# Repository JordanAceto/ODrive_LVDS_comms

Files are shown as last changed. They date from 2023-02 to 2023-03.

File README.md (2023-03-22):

# Set of small PCBs for Odrive ◄► motor encoder comms

- One board sits on an Odrive
- The other goes inside a gimbal motor
- They are connected with twisted pair wire
- The goal is to increase noise immunity and have convenient connectors
- One Odrive board can connect to two encoder boards

---

### Connectors used
- JST GH series 9 pin

---

### IMPORTANT NOTE 1
- The encoder board PCB should be 1mm thick
- The ODRive board can be any thickness you like

---

### IMPORTANT NOTE 2
- The two SN65LVDS050PW chips on the ODrive board will conflict if you use only one motor at a time
- Setting the chip select line high for a given SN65LVDS050PW chip puts its SDI pin into a high impedance state
- If the chip select line is low or not active, the SN65LVDS050PW chip will assert its output on the shared SDI line
- When using only 1 motor there are two options:
  - set the chip select line for the unused SN65LVDS050PW permanently high
  - only solder one SN65LVDS050PW chip

---

### Status
- test build done, safe to order boards

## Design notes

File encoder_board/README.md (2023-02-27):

# encoder_board




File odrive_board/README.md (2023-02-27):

# odrive_board




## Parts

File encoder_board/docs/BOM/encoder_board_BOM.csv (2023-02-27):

# | Reference | Qty | Value | Footprint | DNP
1 | C1 | 1 | 10µF | Capacitor_SMD:C_0603_1608Metric
2 | C2 | 1 | 100nF | Capacitor_SMD:C_0603_1608Metric
3 | C3 | 1 | 100n | Capacitor_SMD:C_0603_1608Metric
4 | C4 | 1 | 1n | Capacitor_SMD:C_0603_1608Metric
5 | J1 | 1 | TO_ODRIVE | Connector_JST:JST_GH_SM09B-GHS-TB_1x09-1MP_P1.25mm_Horizontal
6 | R1 | 1 | 620 | Resistor_SMD:R_0603_1608Metric
7 | R2, R3 | 2 | 110 | Resistor_SMD:R_0603_1608Metric
8 | U1 | 1 | AS5048A | Package_SO:TSSOP-14_4.4x5mm_P0.65mm
9 | U2 | 1 | SN65LVDS050PW | Package_SO:TSSOP-16_4.4x5mm_P0.65mm

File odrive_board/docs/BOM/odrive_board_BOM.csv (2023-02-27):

# | Reference | Qty | Value | Footprint | DNP
1 | C1, C3 | 2 | 100n | Capacitor_SMD:C_0603_1608Metric
2 | C2, C4 | 2 | 1n | Capacitor_SMD:C_0603_1608Metric
3 | J1 | 1 | Odrive_conn | Connector_PinHeader_2.54mm:PinHeader_1x20_P2.54mm_Vertical
4 | J2 | 1 | thru_conn | Connector_PinHeader_2.54mm:PinHeader_1x20_P2.54mm_Vertical
5 | J3 | 1 | MOTOR_0 | Connector_JST:JST_GH_SM09B-GHS-TB_1x09-1MP_P1.25mm_Horizontal
6 | J4 | 1 | MOTOR_1 | Connector_JST:JST_GH_SM09B-GHS-TB_1x09-1MP_P1.25mm_Horizontal
7 | R1, R2 | 2 | 110 | Resistor_SMD:R_0603_1608Metric
8 | TP1 | 1 | SCK | TestPoint:TestPoint_Keystone_5000-5004_Miniature
9 | TP2 | 1 | SDI | TestPoint:TestPoint_Keystone_5000-5004_Miniature
10 | TP3 | 1 | SDO | TestPoint:TestPoint_Keystone_5000-5004_Miniature
11 | TP4 | 1 | CS_0 | TestPoint:TestPoint_Keystone_5000-5004_Miniature
12 | TP5 | 1 | CS_1 | TestPoint:TestPoint_Keystone_5000-5004_Miniature
13 | TP6 | 1 | 3V3 | TestPoint:TestPoint_Keystone_5000-5004_Miniature
14 | TP7 | 1 | GND | TestPoint:TestPoint_Bridge_Pitch5.08mm_Drill0.7mm
15 | U1, U2 | 2 | SN65LVDS050PW | Package_SO:TSSOP-16_4.4x5mm_P0.65mm

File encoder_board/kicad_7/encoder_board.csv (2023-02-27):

# | Reference | Qty | Value | Footprint | DNP
1 | C1 | 1 | 10µF | Capacitor_SMD:C_0603_1608Metric
2 | C2 | 1 | 100nF | Capacitor_SMD:C_0603_1608Metric
3 | C3 | 1 | 4u7 | Capacitor_SMD:C_0603_1608Metric
4 | C4 | 1 | 1u | Capacitor_SMD:C_0603_1608Metric
5 | J1 | 1 | TO_ODRIVE | Connector_JST:JST_GH_SM07B-GHS-TB_1x07-1MP_P1.25mm_Horizontal
6 | R1, R3, R4 | 3 | 620 | Resistor_SMD:R_0603_1608Metric
7 | R2 | 1 | 110 | Resistor_SMD:R_0603_1608Metric
8 | U1 | 1 | AS5048A | Package_SO:TSSOP-14_4.4x5mm_P0.65mm
9 | U2 | 1 | LTC4332 | Package_DFN_QFN:QFN-20-1EP_4x5mm_P0.5mm_EP2.65x3.65mm

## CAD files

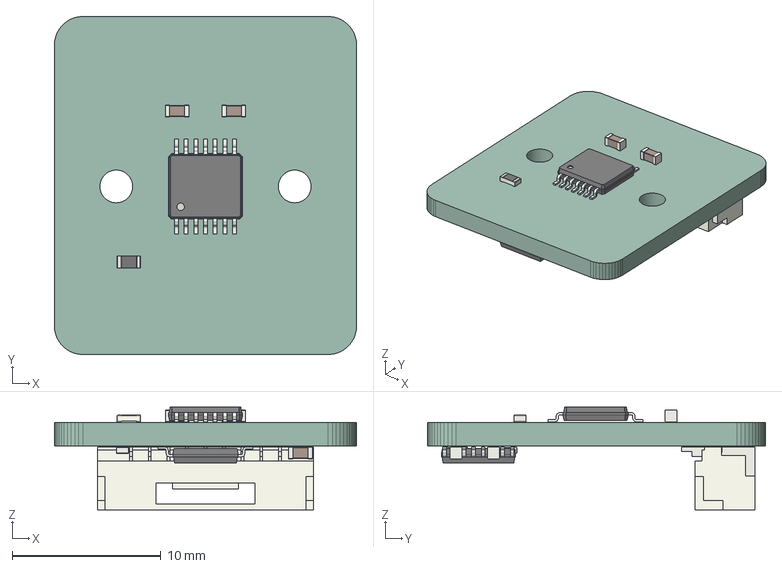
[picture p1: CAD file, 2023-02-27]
encoder_board/docs/3D/encoder_board.step
20.3 x 22.7 x 6.92 mm
PCB

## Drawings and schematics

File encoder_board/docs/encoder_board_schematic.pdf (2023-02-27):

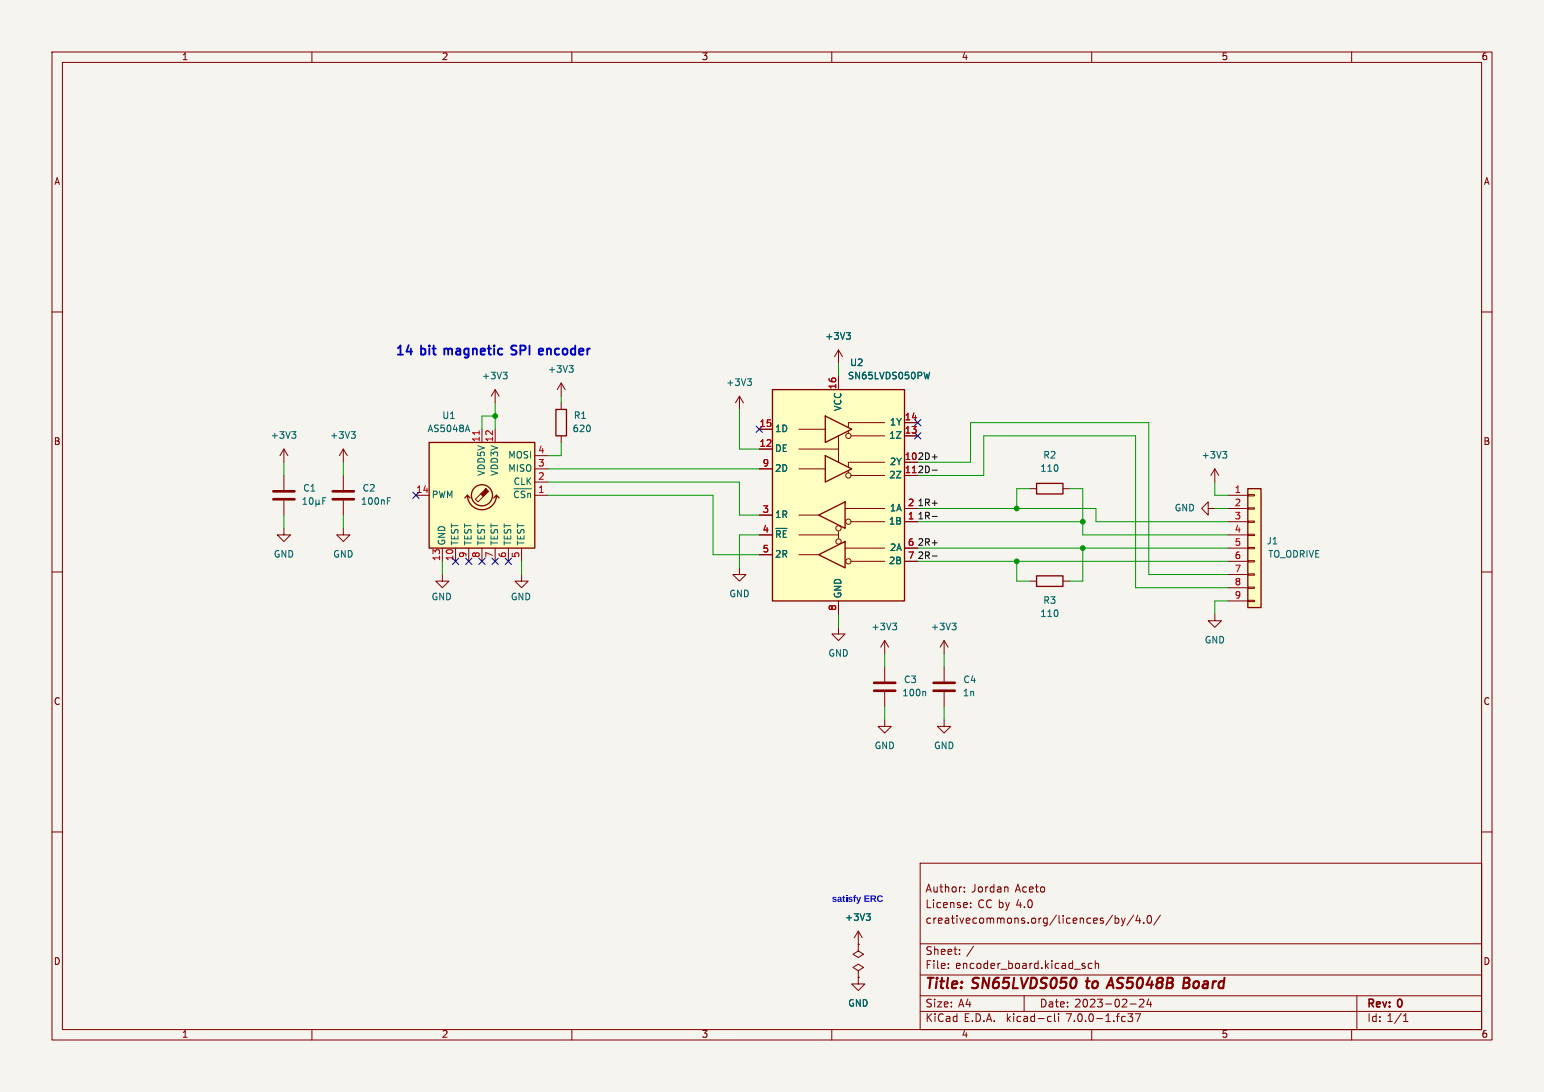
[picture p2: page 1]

Id: 1/1 Title: SN65LVDS050 to AS5048B Board

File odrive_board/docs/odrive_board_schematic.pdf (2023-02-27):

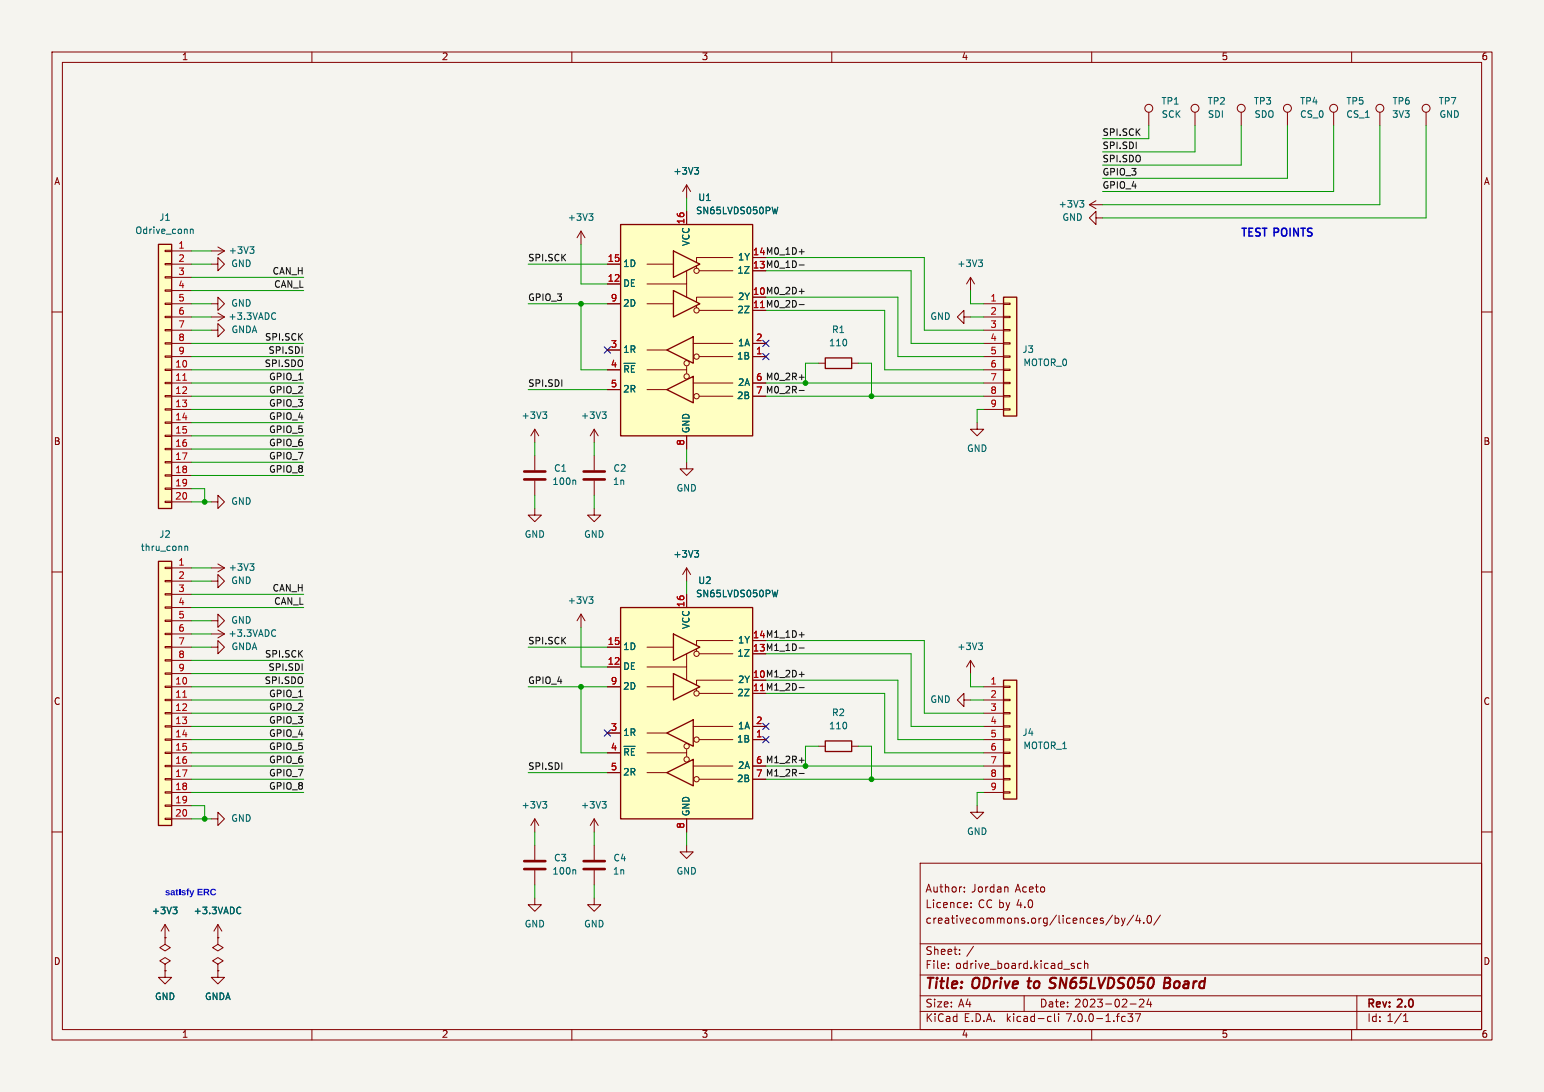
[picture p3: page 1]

GPIO_4 SPI.SCK GPIO_8 SPI.SDO
SPI.SDI M0_2R+ SPI.SDI GPIO_1

Id: 1/1 Title: ODrive to SN65LVDS050 Board

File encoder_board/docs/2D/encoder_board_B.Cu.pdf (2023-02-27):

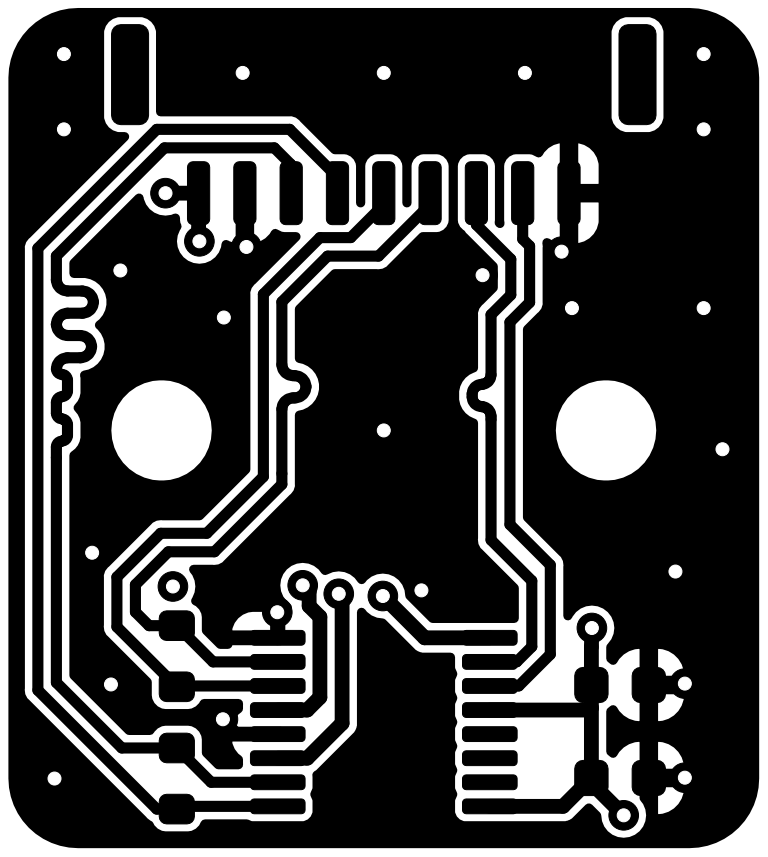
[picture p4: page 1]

Id: 1/1 Title: SN65LVDS050 to AS5048B Board

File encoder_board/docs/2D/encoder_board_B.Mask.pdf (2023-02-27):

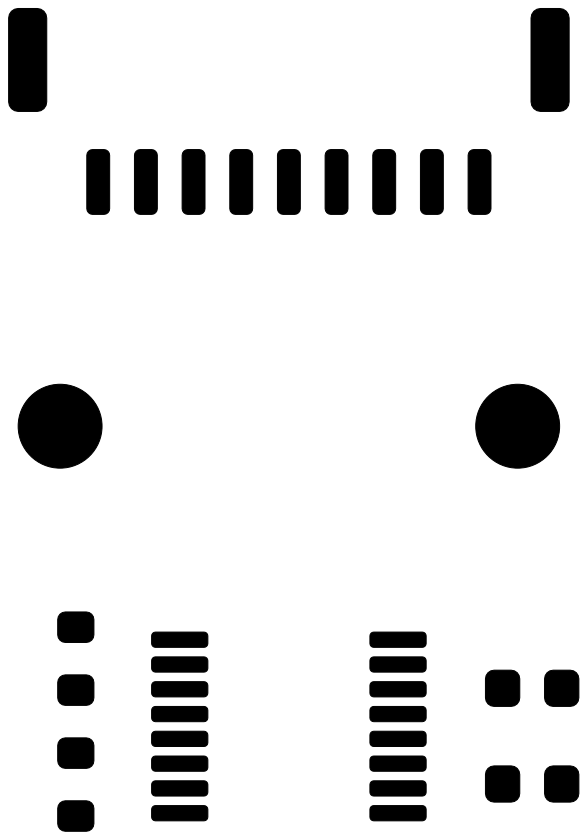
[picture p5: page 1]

Id: 1/1 Title: SN65LVDS050 to AS5048B Board

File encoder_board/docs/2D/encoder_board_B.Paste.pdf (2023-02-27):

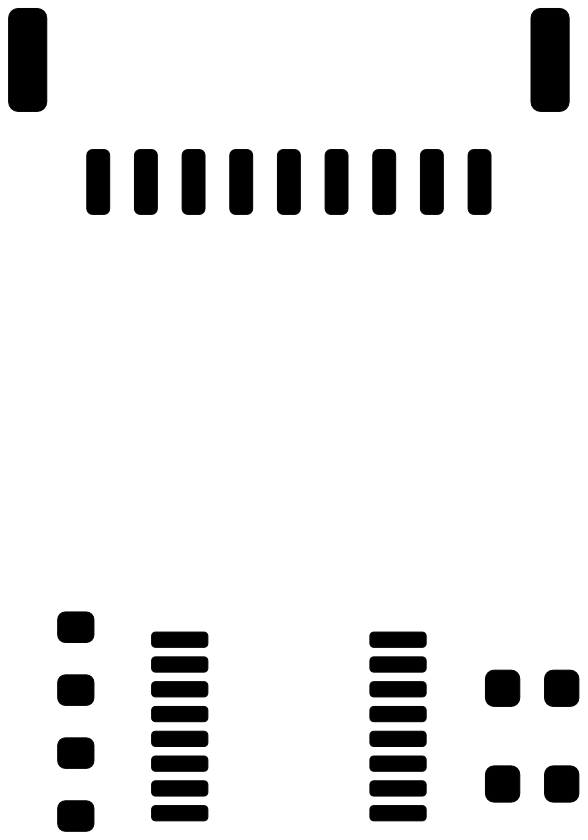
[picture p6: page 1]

Id: 1/1 Title: SN65LVDS050 to AS5048B Board

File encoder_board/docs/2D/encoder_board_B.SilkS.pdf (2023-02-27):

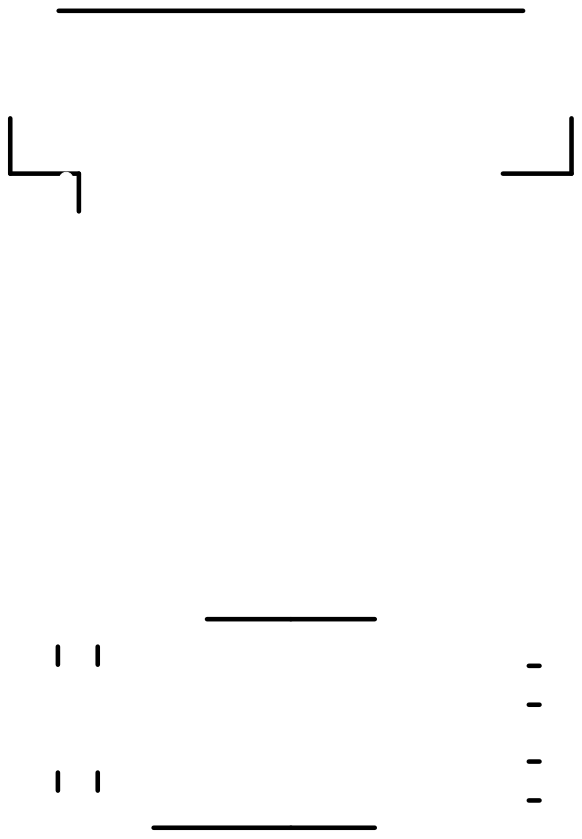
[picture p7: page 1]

Id: 1/1 Title: SN65LVDS050 to AS5048B Board

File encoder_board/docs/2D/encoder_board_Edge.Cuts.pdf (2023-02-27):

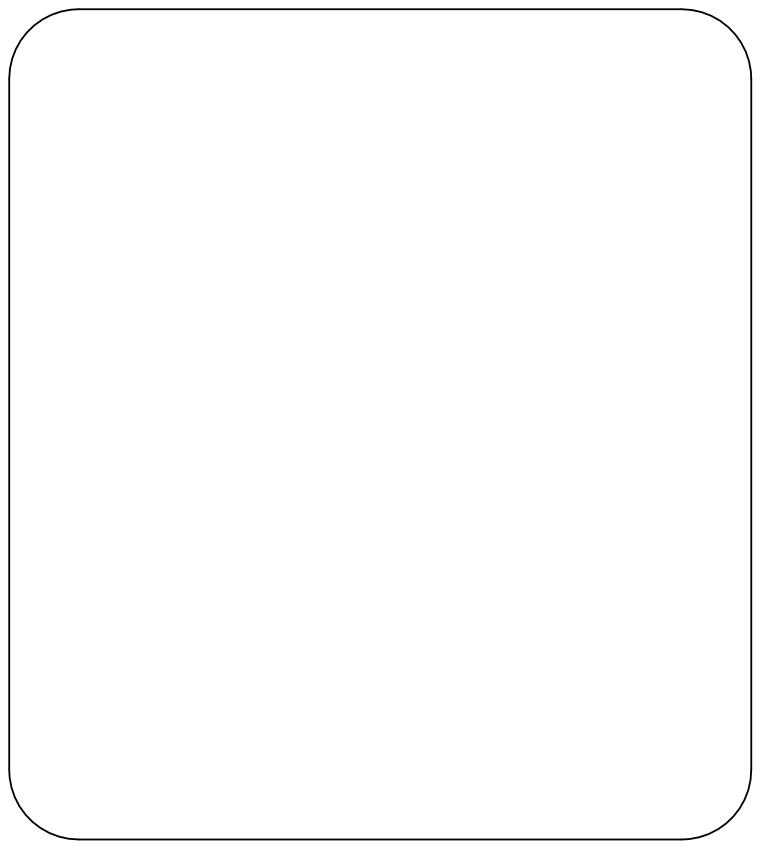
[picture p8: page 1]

Id: 1/1 Title: SN65LVDS050 to AS5048B Board

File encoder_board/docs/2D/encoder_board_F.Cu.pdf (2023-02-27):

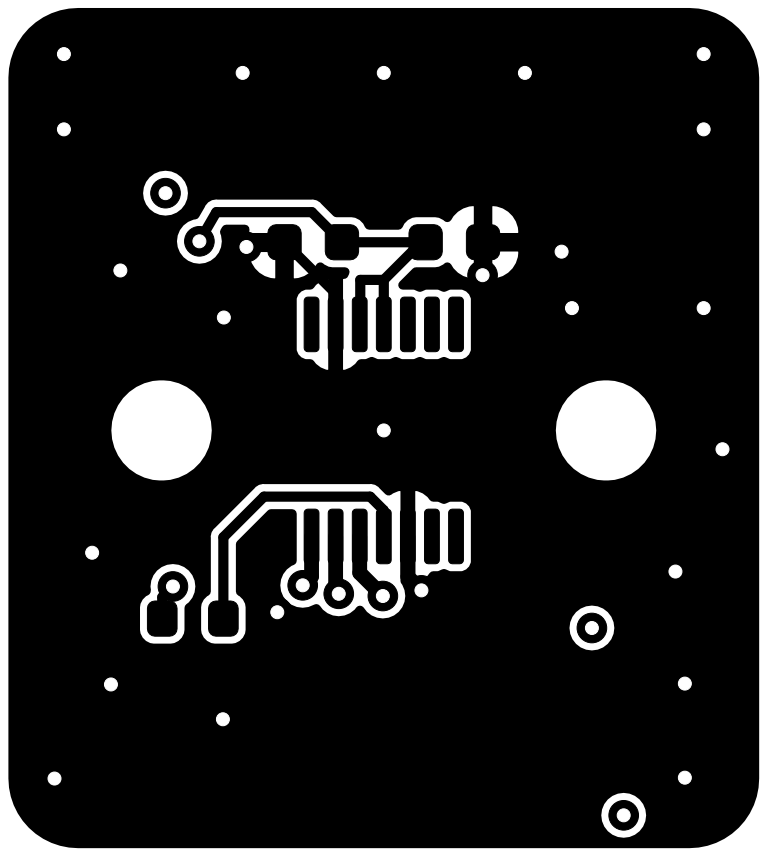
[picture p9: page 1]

Id: 1/1 Title: SN65LVDS050 to AS5048B Board

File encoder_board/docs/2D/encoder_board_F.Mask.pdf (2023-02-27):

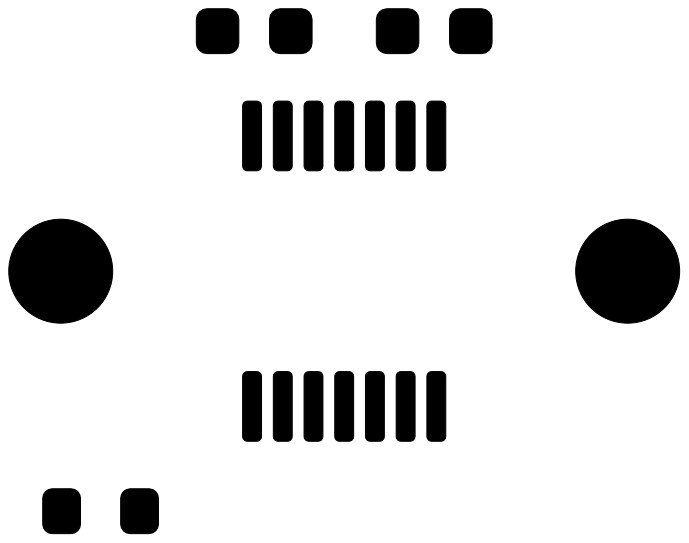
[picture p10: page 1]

Id: 1/1 Title: SN65LVDS050 to AS5048B Board

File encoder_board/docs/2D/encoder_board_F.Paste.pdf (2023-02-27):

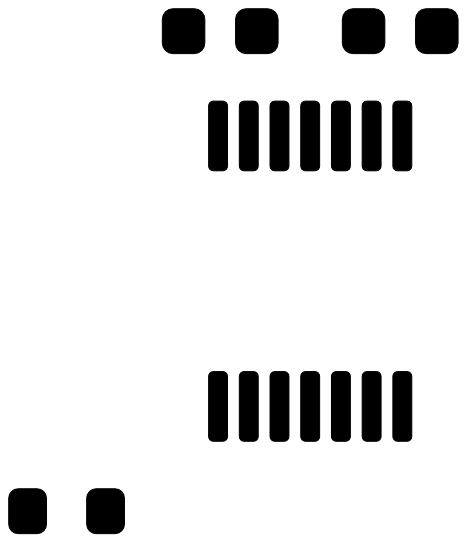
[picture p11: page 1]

Id: 1/1 Title: SN65LVDS050 to AS5048B Board

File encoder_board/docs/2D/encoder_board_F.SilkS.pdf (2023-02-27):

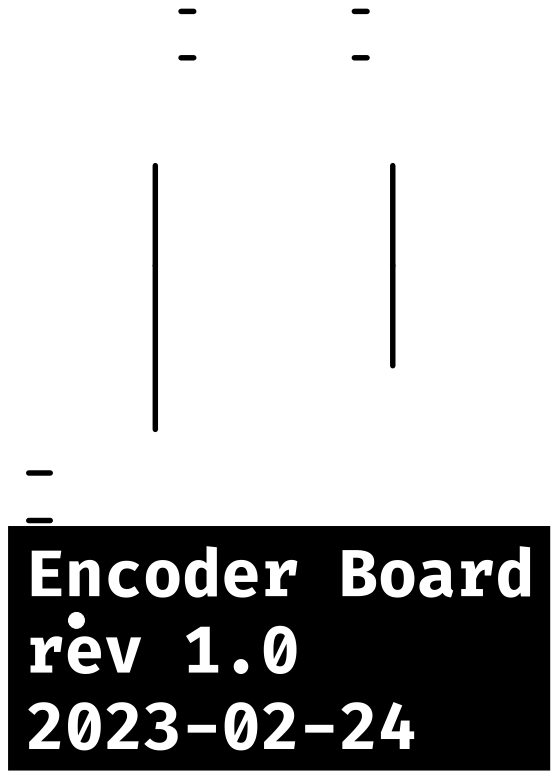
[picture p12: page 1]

Id: 1/1 Title: SN65LVDS050 to AS5048B Board

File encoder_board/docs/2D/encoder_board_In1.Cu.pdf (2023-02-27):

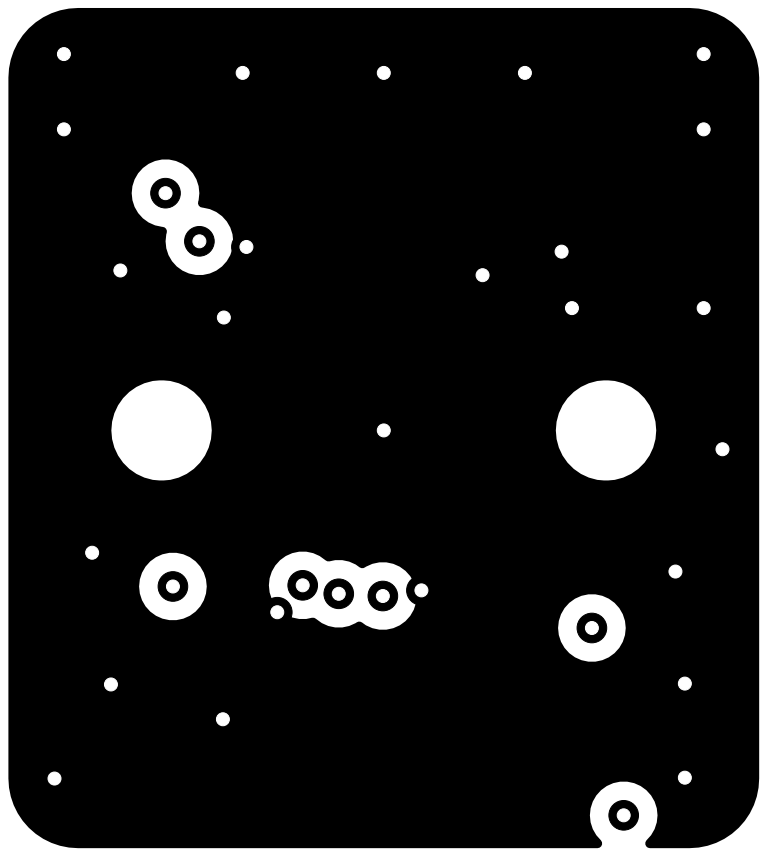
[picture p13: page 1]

Id: 1/1 Title: SN65LVDS050 to AS5048B Board

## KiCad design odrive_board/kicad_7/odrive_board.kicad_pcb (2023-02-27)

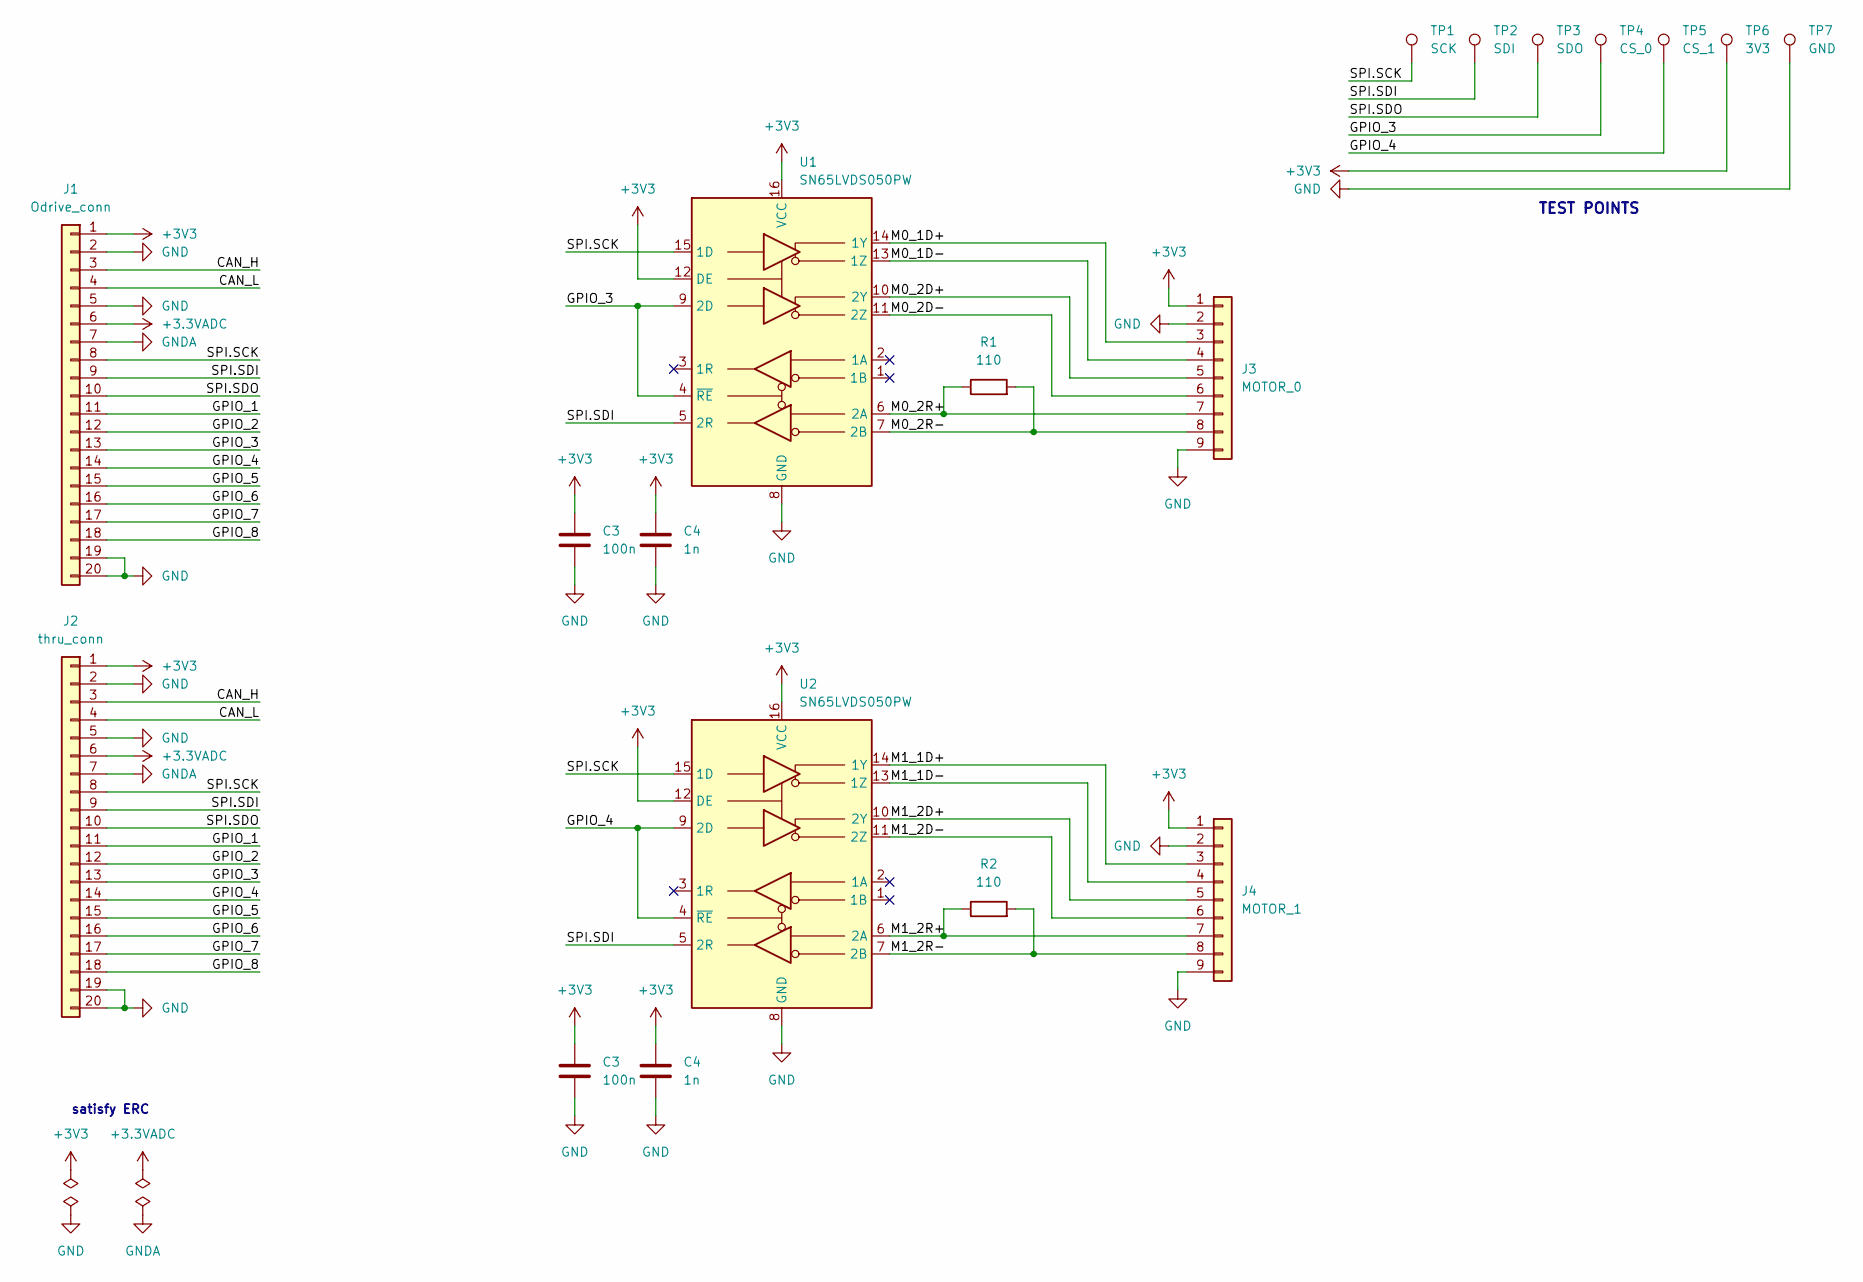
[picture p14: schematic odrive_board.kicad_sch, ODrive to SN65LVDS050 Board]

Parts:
C3: 100n; C_0603_1608Metric
C4: 1n; C_0603_1608Metric
J1: Odrive_conn; PinHeader_1x20_P2.54mm_Vertical
J2: thru_conn; PinHeader_1x20_P2.54mm_Vertical
J3: MOTOR_0; JST_GH_SM09B-GHS-TB_1x09-1MP_P1.25mm_Horizontal
J4: MOTOR_1; JST_GH_SM09B-GHS-TB_1x09-1MP_P1.25mm_Horizontal
R1, R2: 110; R_0603_1608Metric
TP1: SCK; TestPoint_Keystone_5000-5004_Miniature
TP2: SDI; TestPoint_Keystone_5000-5004_Miniature
TP3: SDO; TestPoint_Keystone_5000-5004_Miniature
TP4: CS_0; TestPoint_Keystone_5000-5004_Miniature
TP5: CS_1; TestPoint_Keystone_5000-5004_Miniature
TP6: 3V3; TestPoint_Keystone_5000-5004_Miniature
TP7: GND; TestPoint_Bridge_Pitch5.08mm_Drill0.7mm
U1, U2: SN65LVDS050PW; TSSOP-16_4.4x5mm_P0.65mm

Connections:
+3.3VADC: J1.6, J2.6
+3V3: C3.1, C4.1, J1.1, J2.1, J3.1, J4.1, TP6.1, U1.12 (DE), U1.16 (VCC), U2.12 (DE), U2.16 (VCC); also elsewhere on the board
/CAN_H: J1.3, J2.3
/CAN_L: J1.4, J2.4
/GPIO_1: J1.11, J2.11
/GPIO_2: J1.12, J2.12
/GPIO_3: J1.13, J2.13, TP4.1, U1.4 (~RE), U1.9 (2D)
/GPIO_4: J1.14, J2.14, TP5.1, U2.4 (~RE), U2.9 (2D)
/GPIO_5: J1.15, J2.15
/GPIO_6: J1.16, J2.16
/GPIO_7: J1.17, J2.17
/GPIO_8: J1.18, J2.18
/M0_1D+: J3.3, U1.14 (1Y)
/M0_1D-: J3.4, U1.13 (1Z)
/M0_2D+: J3.5, U1.10 (2Y)
/M0_2D-: J3.6, U1.11 (2Z)
/M0_2R+: J3.7, R1.1, U1.6 (2A)
/M0_2R-: J3.8, R1.2, U1.7 (2B)
/M1_1D+: J4.3, U2.14 (1Y)
/M1_1D-: J4.4, U2.13 (1Z)
/M1_2D+: J4.5, U2.10 (2Y)
/M1_2D-: J4.6, U2.11 (2Z)
/M1_2R+: J4.7, R2.1, U2.6 (2A)
/M1_2R-: J4.8, R2.2, U2.7 (2B)
/SPI.SCK: J1.8, J2.8, TP1.1, U1.15 (1D), U2.15 (1D)
/SPI.SDI: J1.9, J2.9, TP2.1, U1.5 (2R), U2.5 (2R)
/SPI.SDO: J1.10, J2.10, TP3.1
GND: C3.2, C4.2, J1.2, J1.5, J1.19, J1.20, J2.2, J2.5, J2.19, J2.20, J3.2, J3.9, J4.2, J4.9, TP7.1, U1.8 (GND), U2.8 (GND); also elsewhere on the board
GNDA: J1.7, J2.7

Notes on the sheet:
satisfy ERC
TEST POINTS

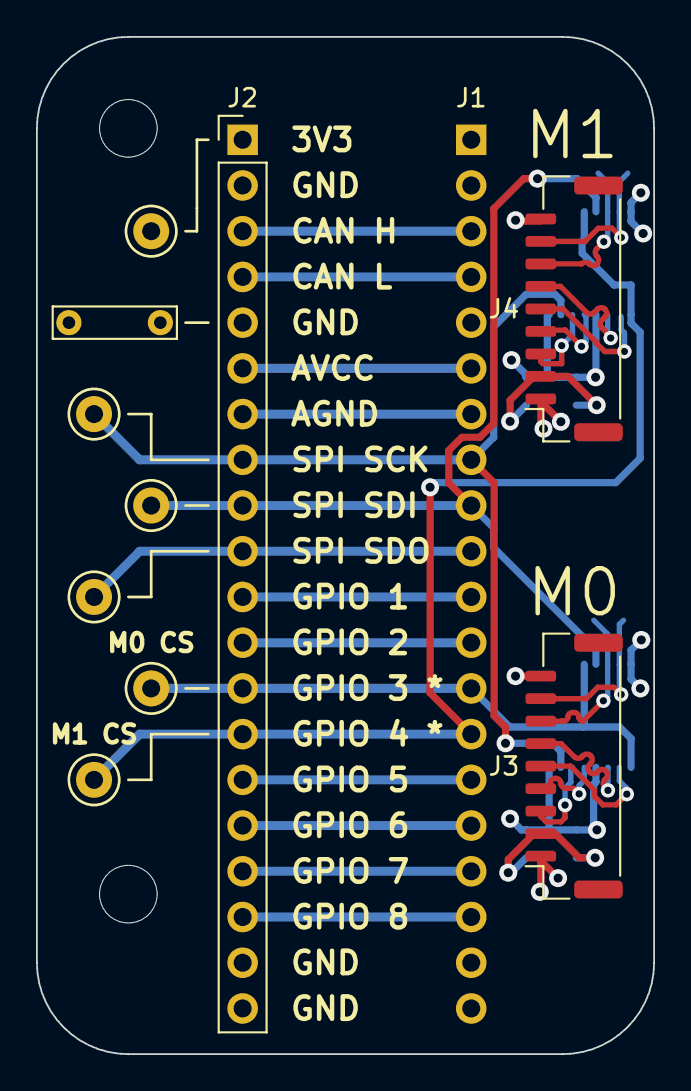
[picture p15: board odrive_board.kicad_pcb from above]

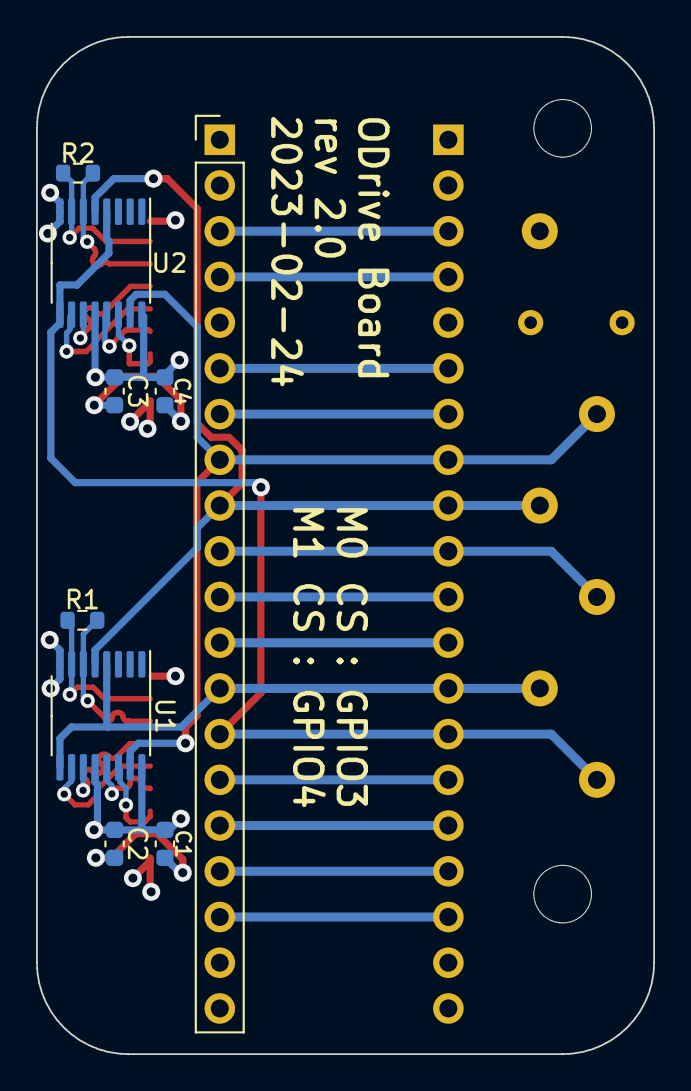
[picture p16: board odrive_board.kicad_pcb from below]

Board: 4 copper layers, 34.3 x 56.5 mm, 19 parts (9 on the bottom side), 29 nets.

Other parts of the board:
C1: 100n; C_0603_1608Metric
C2: 1n; C_0603_1608Metric

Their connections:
+3V3: C1.1, C2.1; also elsewhere on the board
GND: C1.2, C2.2; also elsewhere on the board

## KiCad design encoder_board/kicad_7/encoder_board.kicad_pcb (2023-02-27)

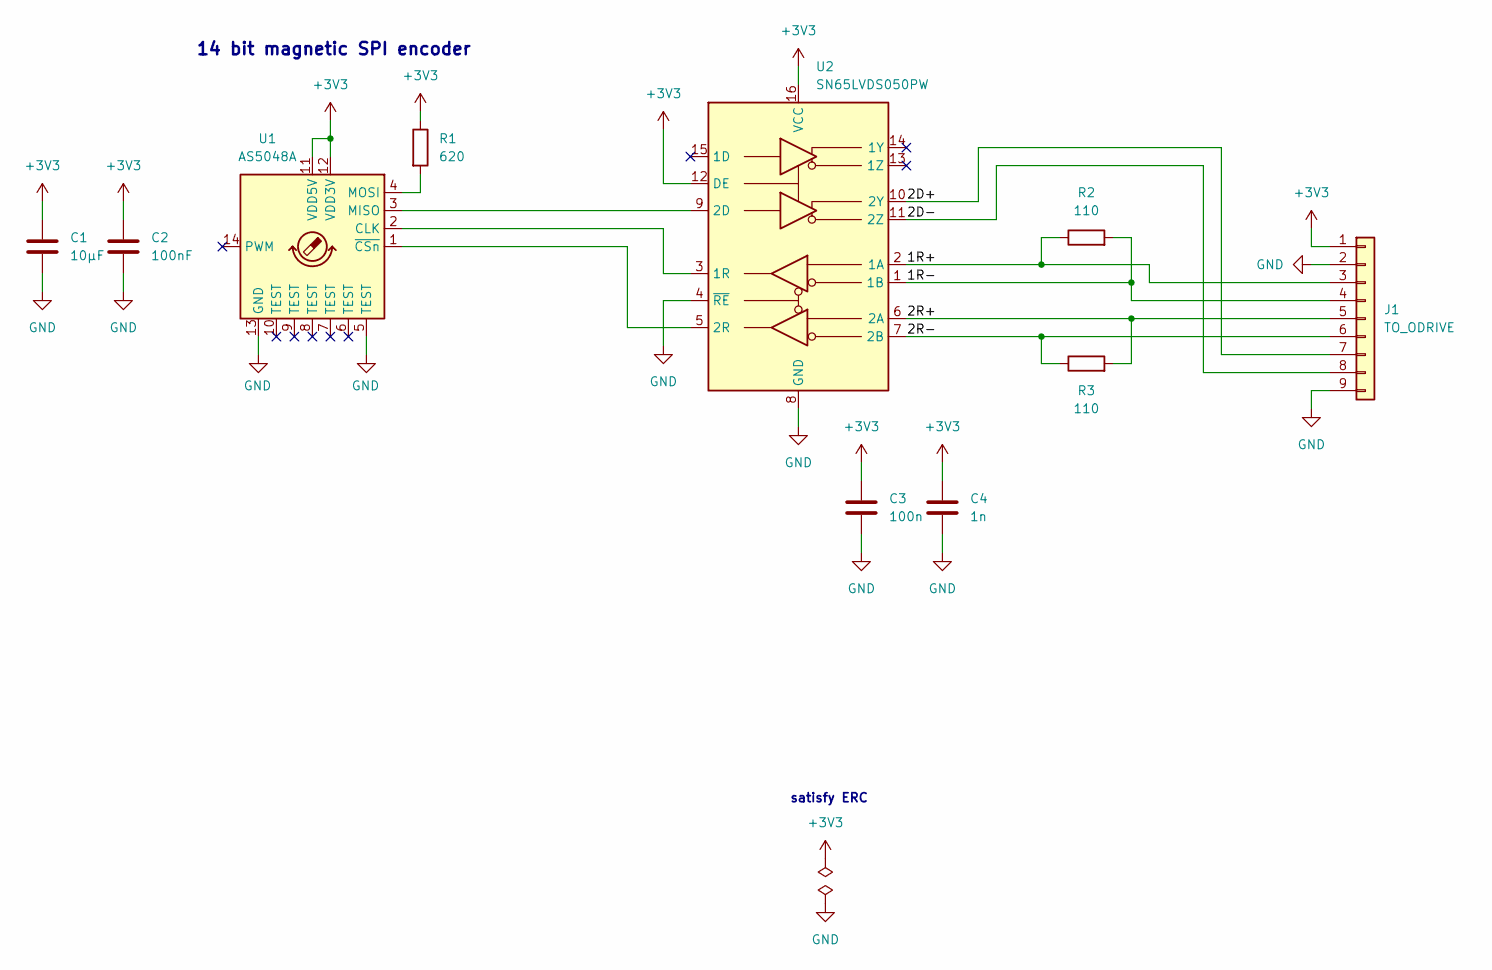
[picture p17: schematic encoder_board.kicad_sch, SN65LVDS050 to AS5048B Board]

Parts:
C1: 10µF; C_0603_1608Metric
C2: 100nF; C_0603_1608Metric
C3: 100n; C_0603_1608Metric
C4: 1n; C_0603_1608Metric
J1: TO_ODRIVE; JST_GH_SM09B-GHS-TB_1x09-1MP_P1.25mm_Horizontal
R1: 620; R_0603_1608Metric
R2, R3: 110; R_0603_1608Metric
U1: AS5048A; TSSOP-14_4.4x5mm_P0.65mm; Part AS5048A
U2: SN65LVDS050PW; TSSOP-16_4.4x5mm_P0.65mm

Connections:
+3V3: C1.1, C2.1, C3.1, C4.1, J1.1, R1.1, U1.11 (VDD5V), U1.12 (VDD3V), U2.12 (DE), U2.16 (VCC)
/1R+: J1.3, R2.1, U2.2 (1A)
/1R-: J1.4, R2.2, U2.1 (1B)
/2D+: J1.7, U2.10 (2Y)
/2D-: J1.8, U2.11 (2Z)
/2R+: J1.5, R3.2, U2.6 (2A)
/2R-: J1.6, R3.1, U2.7 (2B)
GND: C1.2, C2.2, C3.2, C4.2, J1.2, J1.9, U1.5 (TEST), U1.13 (GND), U2.4 (~RE), U2.8 (GND)
unnamed: U1.2 (CLK), U2.3 (1R)
unnamed: U1.3 (MISO), U2.9 (2D)
unnamed: R1.2, U1.4 (MOSI)
unnamed: U1.1 (~CSn), U2.5 (2R)

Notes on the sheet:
14 bit magnetic SPI encoder
satisfy ERC

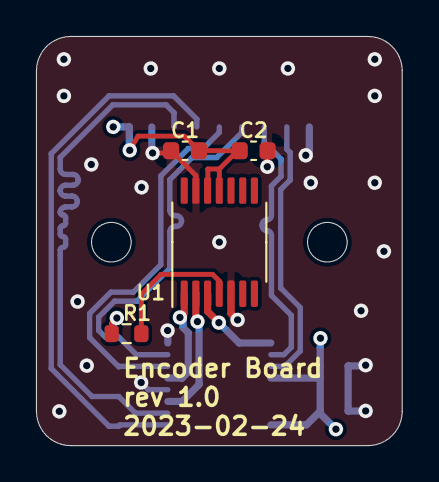
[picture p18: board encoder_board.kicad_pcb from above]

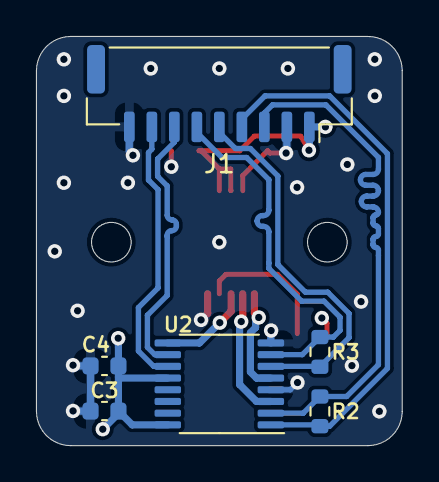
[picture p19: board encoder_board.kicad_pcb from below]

Board: 4 copper layers, 20.3 x 22.7 mm, 12 parts (6 on the bottom side), 12 nets.

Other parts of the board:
H1, H2: MountingHole; MountingHole_2.2mm_M2

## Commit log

2023-02-27 Add note about encoder thickness
2023-02-27 Add missing drill files to compressed gerbers

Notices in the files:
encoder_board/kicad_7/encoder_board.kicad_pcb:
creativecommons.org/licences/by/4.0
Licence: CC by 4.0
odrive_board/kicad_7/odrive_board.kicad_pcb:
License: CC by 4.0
